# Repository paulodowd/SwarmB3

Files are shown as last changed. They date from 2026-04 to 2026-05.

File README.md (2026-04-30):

# SwarmB3

Working on Swarm Board version 3... so I decided the tinkering hadn't finished yet :)

Currently work in progress.  
- PCB in testing, version 4.
- Initial code drafted but a mess.

## Development Notes

**14/04/26:** Lots and lots of debugging between hardware and software.  The pcb design worked on the assumption that the UART tx could be inverted in software, as stated in the SAMD51 datasheet.  However, it doesn't work as I expected.  It seems to invert the data, but the idle state remains high.  This causes issues for IR communication because I don't want to saturate the environment with the carrier wave whilst communication is not occuring (idle high, AND'd with clock -> constant carrier wave transmission). I tried a software fix, pulling the gpio low between transmissions.  However, I can't seem to restore the GPIO properly without messing up the protocol overall. I got as far as seeing the bit pattern shifted by 1 bit, which is occuring because the receiver is mis-registering the start bit.  I tried leaving the GPIO alone, and only enabling/disabling the carrier wave, but the same problem is occuring.  When I look at both sides of the communication on the oscilloscope, I can see that for a batch send (like 10 bytes), the first byte is dropping the start bit.  I haven't been able to get to the bottom of why.  If I do not invert the tx, the problem goes away, but I don't want a non-inverted signal (saturation problem).  It could be that the essential problem is that inverting the Tx in SAMD51 doesn't invert the start and stop bits - the datasheet is unclear.  It simply says "start and stop unchanged", and I'm not sure if that means overall functionality or logic polarity.  It seems like the latter.  I tried some other logic gates.  Surprisingly, 74hc32 (OR) works as a drop in - however, it does mean that for data logic 1, the data stream is always on, and for data logic 0 actually an on/off pulse train - which is not ideal.  The receiver seems quite robust to this, the datasheet has measures for this sort of thing.  However, I don't want a board that could cause communication defects alongside from what I am investigating in research.  A possible fix is to implement active low LED drivers, which would necessitate an extra transister per UART (e.g. +4).  I don't fancy soldering that, so instead I've updated the pcb to pass tx outputs through a 74hc14 first.  I've tested this on breadboard and it works fine.  It means I can just use the UART interfaces normally without any software SAMD51 inversion.  The current code (ItsyBitsy_test) is a mess from all my debugging chopping and changes.  I'll refactor after testing the new pcb when it arrives.

**10/04/26:** The TSDP34156 is active low output when receiving an IR burst.  I had thought I would use the M4 SERCOM interface to invert the UART signal logic.  It seems like only the start,stop and data are inverted, but the idle signal remains high in either case. I spent some time trying to find a software solution to pull the tx line low, with no luck.  Even with no idle, or long bursts of transmission, I was getting gibberish on the receiving end regardless of whether I was inverting Tx or not.  With the assumption of inverting in software, the first pcb design had a 74hc08 AND gate to combine the 58khz clock and data.  Abandoning this, I first tried a NAND, but that actually just negates the effect of the clock - since a changing clock qualifies as not-and against data or no data.  Instead, an OR gate works. With Tx not inverted, if I draw out the truth table, then it means that for a data logic 0 a 58khz burst is created, and for data logic 1 a constant IR signal is made (not modulated, just on).     

**08/04/26:** Some pretty annoying problems with the first PCB prototype!  The 74hc08 ground was isolated.  The pots for current limiting were not in logical physical locations, not next to their LEDs.  I labelled the ItsyBitsy pin 7 wrong, so it wasn't conencted to the 74hc08.  Fixed all of that.  I've installed two different types of IR LEDs to compare the difference.  One is the Vishay TSAL4400 (https://www.vishay.com/en/product/81006/), and the other is an Onsemi QEE113 (https://www.onsemi.com/products/interfaces/infrared/emitting-diodes/qee113).  Both have similar characteristics, slightly different radiance patterns. I prefer the form factor of the Onsemi device.

**27/03/26:** Using the Adafruit SAMD51 board config, they have a wrapped class named sercom around the original defintions SERCOM (difference being lower and upper case).  I wanted to invert Tx (maybe Rx) and the Adafruit wrapper hasn't got this implemented yet.  These are useful links for low level structures and definitions for SERCOM (SAMD51 in general).
- https://github.com/ace22293/SAMD51/tree/master
- https://github.com/arduino/ArduinoCore-samd/tree/master/cores/arduino
- https://github.com/arduino/ArduinoModule-CMSIS-Atmel/tree/master/CMSIS-Atmel/CMSIS/Device/ATMEL/samd51/include/instance
- https://github.com/arduino/ArduinoModule-CMSIS-Atmel/tree/master/CMSIS-Atmel/CMSIS/Device/ATMEL/samd51/include

- **25/03/26:** Started the design of version 3 of the swarm board.  The plan is to use the Adafruit ItsyBitsy M4, providing a hardware UART interface for each IR reciever on the pcb. When drafting this PCB, I couldn't find a convenient symbol or footprint, so I've used two rows of pin headers and labels.  I also noticed that the symbol for the double row header for the M5Stack Core2 doesn't correspond with the physical footprint - but the enumeration is correct (just a bit confusing).

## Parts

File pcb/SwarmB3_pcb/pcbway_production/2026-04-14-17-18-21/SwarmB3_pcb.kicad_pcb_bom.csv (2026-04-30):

Designator | Quantity | Value | Footprint | Package | MPN | DNP | Mount_Type | Description | PROD_ID | Voltage | Tolerance | Field4
C1, C2 | 2 | 0.1uF | C_Disc_D4.7mm_W2.5mm_P5.00mm |  |  |  | tht | Unpolarized capacitor | CAP-25565 | 16V | 10%
D1_B1, D2_A1, D2_B1, D3_A1, D3_B1, D4_A1, D4_B1, D_1A1 | 8 | IR_LED | LED_D3.0mm_Horizontal_O1.27mm_Z2.0mm |  |  |  | tht
J1 | 1 | 5v_3Pi | PinHeader_1x02_P2.54mm_Vertical |  |  |  | tht |  |  |  |  | CONN-09863
J10 | 1 | ItsyBitsyRight | PinHeader_1x14_P2.54mm_Vertical |  |  |  | tht | Generic connector, single row, 01x14, script generated
J11 | 1 | ItsyBitsyLeft | PinHeader_1x14_P2.54mm_Vertical |  |  |  | tht | Generic connector, single row, 01x14, script generated
J2 | 1 | GND_3Pi | PinHeader_1x02_P2.54mm_Vertical |  |  |  | tht |  |  |  |  | CONN-09863
J3 | 1 | I2C_3V3_Exp | PinHeader_1x04_P2.54mm_Vertical |  |  |  | tht
J4 | 1 | Conn_02x15_M5Stack_Core2 | PinHeader_2x15_P2.54mm_Vertical |  |  |  | tht
J5 | 1 | I2C_3Pi | PinHeader_1x02_P2.54mm_Vertical |  |  |  | tht |  |  |  |  | CONN-09863
J6 | 1 | 3PI_SWTCH | PinHeader_1x02_P2.54mm_Vertical |  |  |  | tht |  |  |  |  | CONN-09863
J8 | 1 | ProxA | PinHeader_1x04_P2.54mm_Vertical |  |  |  | tht
J9 | 1 | ProxB | PinHeader_1x04_P2.54mm_Vertical |  |  |  | tht
PWR1, RESET1 | 2 | Bttn | SW_PUSH_6mm |  |  |  | tht
Q1, Q2, Q3, Q5 | 4 | PN2222A | TO-92_Inline |  |  |  | tht | 1A Ic, 40V Vce, NPN Transistor, General Purpose Transistor, TO-92
Q7, Q8 | 2 | 2N7000 | TO-92_Inline |  |  |  | tht
R1, R10, R13, R9 | 4 | 82R | R_Axial_DIN0204_L3.6mm_D1.6mm_P7.62mm_Horizontal |  |  |  | tht
R15, R16, R17, R18 | 4 | 1K | R_Axial_DIN0204_L3.6mm_D1.6mm_P7.62mm_Horizontal |  |  |  | tht
R19, R20 | 2 | 4k7 | R_Axial_DIN0204_L3.6mm_D1.6mm_P7.62mm_Horizontal |  |  |  | tht
R2, R3, R6 | 3 | LDR | R_LDR_5.0x4.1mm_P3mm_Vertical |  |  |  | tht
R4, R5, R7 | 3 | 10K_LDR | R_Axial_DIN0204_L3.6mm_D1.6mm_P7.62mm_Horizontal |  |  |  | tht
U1 | 1 | 74HC14 | DIP-14_W7.62mm_Socket |  |  |  | tht | Hex inverter schmitt trigger
U2 | 1 | 74LS08 | DIP-14_W7.62mm_Socket |  |  |  | tht | Quad And2
UD_1, UD_2, UD_3, UD_4 | 4 | TSDP34138 | Vishay_MOLD-3Pin |  |  |  | tht
VR2_A1, VR3_A1, VR4_A1, VR_1A1 | 4 | 5K_Pot_IRLED | Potentiometer_Bourns_3386P_Vertical |  |  |  | tht |  |  |  |  | RES-09730

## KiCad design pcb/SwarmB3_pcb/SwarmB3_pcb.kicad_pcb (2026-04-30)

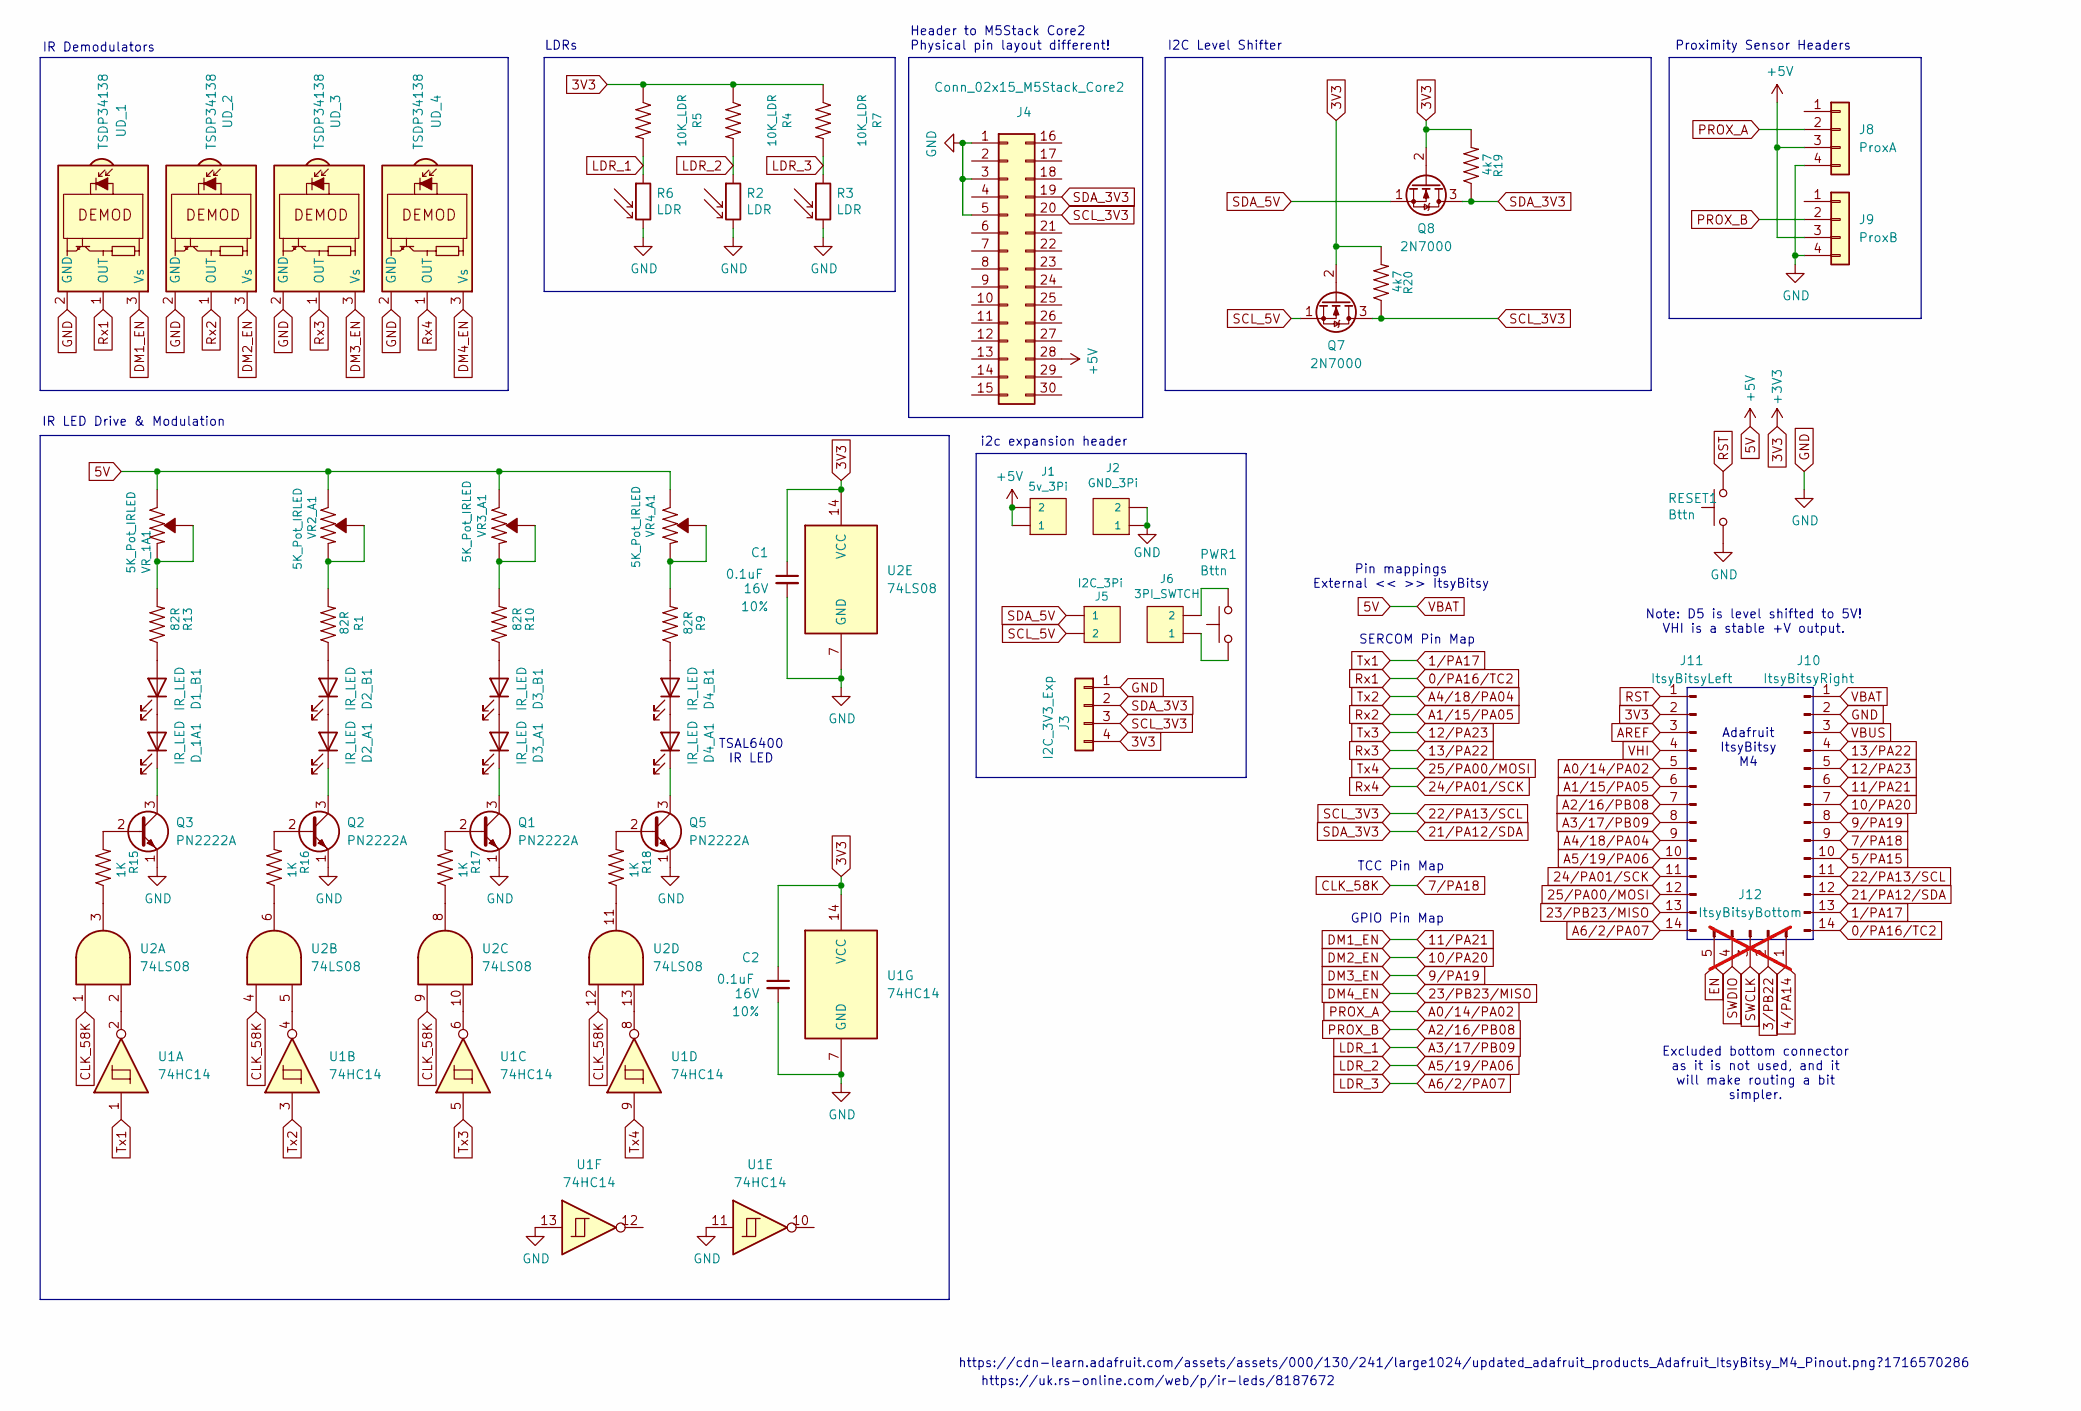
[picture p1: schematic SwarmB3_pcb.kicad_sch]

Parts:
C1, C2: 0.1uF; C_Disc_D4.7mm_W2.5mm_P5.00mm; Voltage 16V; Tolerance 10%
D1_B1, D2_A1, D2_B1, D3_A1, D3_B1, D4_A1, D4_B1: IR_LED; LED_D3.0mm_Horizontal_O1.27mm_Z2.0mm
D_1A1: IR_LED; LED_D3.0mm_Horizontal_O1.27mm_Z2.0mm
J1: 5v_3Pi; PinHeader_1x02_P2.54mm_Vertical
J2: GND_3Pi; PinHeader_1x02_P2.54mm_Vertical
J3: I2C_3V3_Exp; PinHeader_1x04_P2.54mm_Vertical
J4: Conn_02x15_M5Stack_Core2; PinHeader_2x15_P2.54mm_Vertical
J5: I2C_3Pi; PinHeader_1x02_P2.54mm_Vertical
J6: 3PI_SWTCH; PinHeader_1x02_P2.54mm_Vertical
J8: ProxA; PinHeader_1x04_P2.54mm_Vertical
J9: ProxB; PinHeader_1x04_P2.54mm_Vertical
J10: ItsyBitsyRight; PinHeader_1x14_P2.54mm_Vertical
J11: ItsyBitsyLeft; PinHeader_1x14_P2.54mm_Vertical
J12: ItsyBitsyBottom; not fitted
PWR1: Bttn; SW_PUSH_6mm
Q1, Q2, Q3, Q5: PN2222A; TO-92_Inline
Q7, Q8: 2N7000; TO-92_Inline
R1, R9, R10, R13: 82R; R_Axial_DIN0204_L3.6mm_D1.6mm_P7.62mm_Horizontal
R2, R3, R6: LDR; R_LDR_5.0x4.1mm_P3mm_Vertical
R4, R5, R7: 10K_LDR; R_Axial_DIN0204_L3.6mm_D1.6mm_P7.62mm_Horizontal
R15, R16, R17, R18: 1K; R_Axial_DIN0204_L3.6mm_D1.6mm_P7.62mm_Horizontal
R19, R20: 4k7; R_Axial_DIN0204_L3.6mm_D1.6mm_P7.62mm_Horizontal
RESET1: Bttn; SW_PUSH_6mm
U1: 74HC14; DIP-14_W7.62mm_Socket
U2: 74LS08; DIP-14_W7.62mm_Socket
UD_1, UD_2, UD_3, UD_4: TSDP34138; Vishay_MOLD-3Pin
VR2_A1, VR3_A1, VR4_A1: 5K_Pot_IRLED; Potentiometer_Bourns_3386P_Vertical
VR_1A1: 5K_Pot_IRLED; Potentiometer_Bourns_3386P_Vertical

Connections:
0/PA16/TC2: J10.14, UD_1.1 (OUT)
1/PA17: J10.13, U1.1
3V3: C1.1, C2.1, J3.4, J11.2, Q7.2 (G), Q8.2 (G), R4.1, R5.1, R7.1, R19.2, R20.2, U1.14 (VCC), U2.14 (VCC)
5V: J1.1, J1.2, J4.28, J8.3, J9.3, J10.1, VR2_A1.3 (CW), VR3_A1.3 (CW), VR4_A1.3 (CW), VR_1A1.3 (CW)
5/PA15: J10.10
7/PA18: J10.9, U2.1, U2.4, U2.9, U2.12
9/PA19: J10.8, UD_3.3 (Vs)
10/PA20: J10.7, UD_2.3 (Vs)
11/PA21: J10.6, UD_1.3 (Vs)
12/PA23: J10.5, U1.5
13/PA22: J10.4, UD_3.1 (OUT)
21/PA12/SDA: J3.2, J4.19, J10.12, Q8.3 (D), R19.1
22/PA13/SCL: J3.3, J4.20, J10.11, Q7.3 (D), R20.1
23/PB23/MISO: J11.13, UD_4.3 (Vs)
24/PA01/SCK: J11.11, UD_4.1 (OUT)
25/PA00/MOSI: J11.12, U1.9
A0/14/PA02: J8.2, J11.5
A1/15/PA05: J11.6, UD_2.1 (OUT)
A2/16/PB08: J9.2, J11.7
A3/17/PB09: J11.8, R5.2, R6.1
A4/18/PA04: J11.9, U1.3
A5/19/PA06: J11.10, R2.1, R4.2
A6/2/PA07: J11.14, R3.1, R7.2
AREF: J11.3
GND: C1.2, C2.2, J2.1, J2.2, J3.1, J4.1, J4.3, J4.5, J8.4, J9.4, J10.2, Q1.1 (E), Q2.1 (E), Q3.1 (E), Q5.1 (E), R2.2, R3.2, R6.2, RESET1.1, U1.7 (GND), U1.11, U1.13, U2.7 (GND), UD_1.2 (GND), UD_2.2 (GND), UD_3.2 (GND), UD_4.2 (GND)
unnamed: D1_B1.2 (A), R13.1
unnamed: D1_B1.1 (K), D_1A1.2 (A)
unnamed: D2_A1.2 (A), D2_B1.1 (K)
unnamed: D2_A1.1 (K), Q2.3 (C)
unnamed: D2_B1.2 (A), R1.1
unnamed: D3_A1.2 (A), D3_B1.1 (K)
unnamed: D3_A1.1 (K), Q1.3 (C)
unnamed: D3_B1.2 (A), R10.1
unnamed: D4_A1.2 (A), D4_B1.1 (K)
unnamed: D4_A1.1 (K), Q5.3 (C)
unnamed: D4_B1.2 (A), R9.1
unnamed: D_1A1.1 (K), Q3.3 (C)
unnamed: J6.1, PWR1.1
unnamed: J6.2, PWR1.2
unnamed: Q1.2 (B), R17.2
unnamed: Q2.2 (B), R16.2
unnamed: Q3.2 (B), R15.2
unnamed: Q5.2 (B), R18.2
unnamed: R15.1, U2.3
unnamed: R16.1, U2.6
unnamed: R17.1, U2.8
unnamed: R18.1, U2.11
unnamed: U1.2, U2.2
unnamed: U1.4, U2.5
unnamed: U1.6, U2.10
unnamed: U1.8, U2.13
unnamed: R1.2, VR2_A1.1 (CCW), VR2_A1.2 (WIPER)
unnamed: R10.2, VR3_A1.1 (CCW), VR3_A1.2 (WIPER)
unnamed: R9.2, VR4_A1.1 (CCW), VR4_A1.2 (WIPER)
unnamed: R13.2, VR_1A1.1 (CCW), VR_1A1.2 (WIPER)
RST: J11.1, RESET1.2
SCL_5V: J5.2, Q7.1 (S)
SDA_5V: J5.1, Q8.1 (S)
VBUS: J10.3
VHI: J11.4

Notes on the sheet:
IR LED Drive & Modulation
IR Demodulators
Pin mappings External << >> ItsyBitsy
Proximity Sensor Headers
GPIO Pin Map
I2C Level Shifter
Adafruit ItsyBitsy M4
SERCOM Pin Map
Header to M5Stack Core2 Physical pin layout different!
https://uk.rs-online.com/web/p/ir-leds/8187672
TCC Pin Map
Note: D5 is level shifted to 5V! VHI is a stable +V output.
https://cdn-learn.adafruit.com/assets/assets/000/130/241/large1024/updated_adafruit_products_Adafruit_ItsyBitsy_M4_Pinout.png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
LDRs
Excluded bottom connector as it is not used, and it will make routing a bit simpler.
i2c expansion header
TSAL6400 IR LED

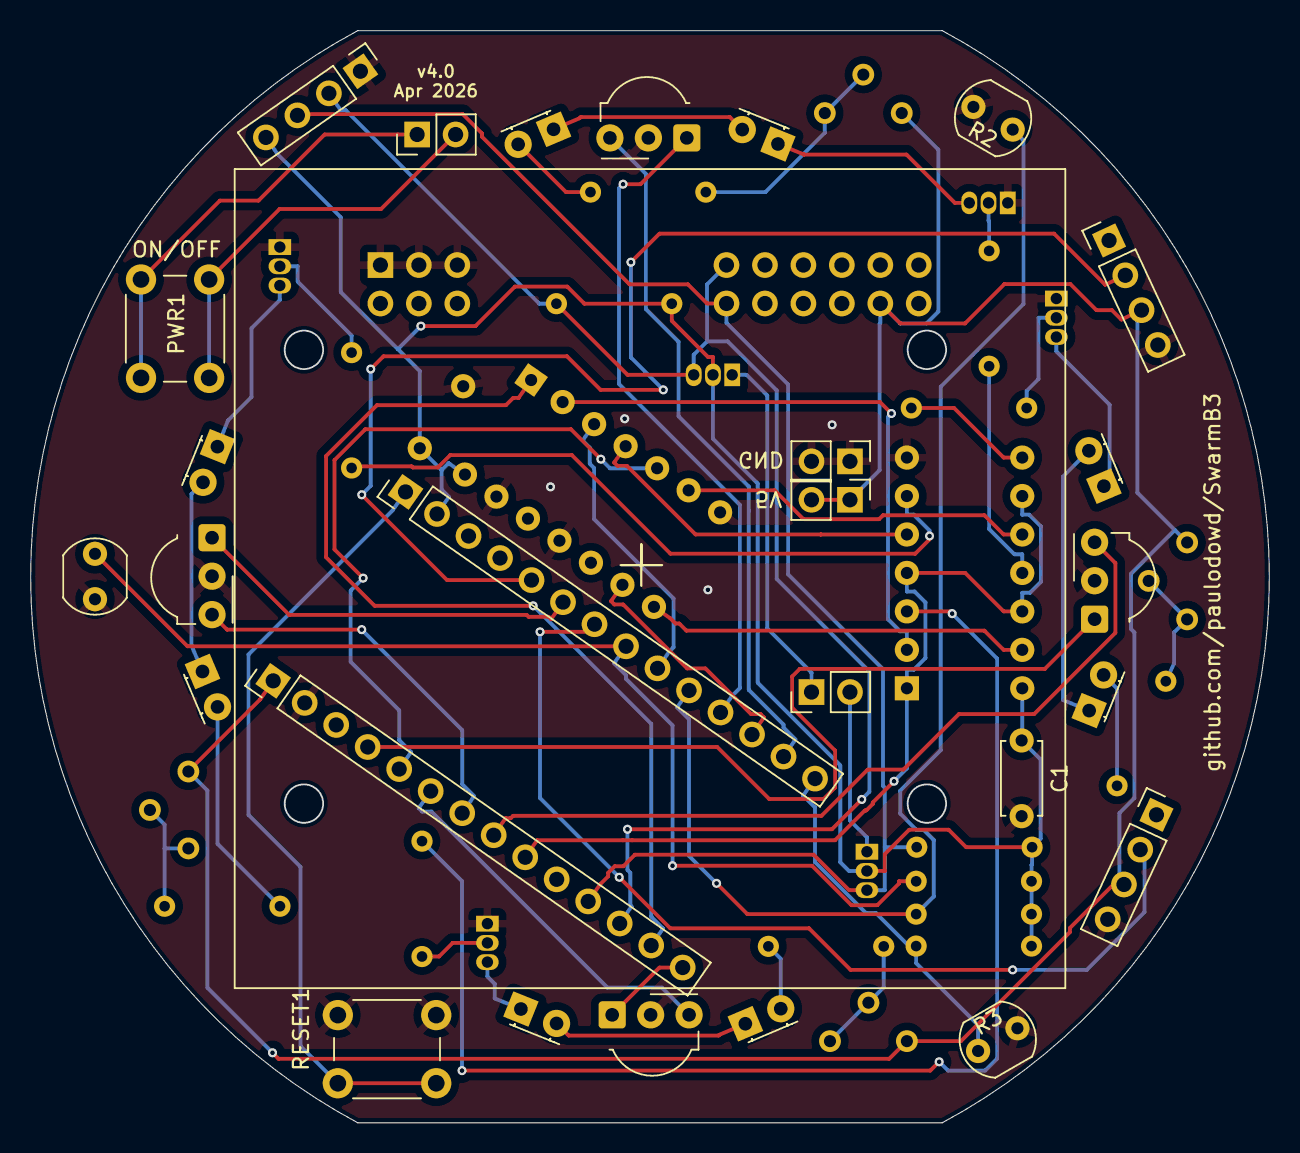
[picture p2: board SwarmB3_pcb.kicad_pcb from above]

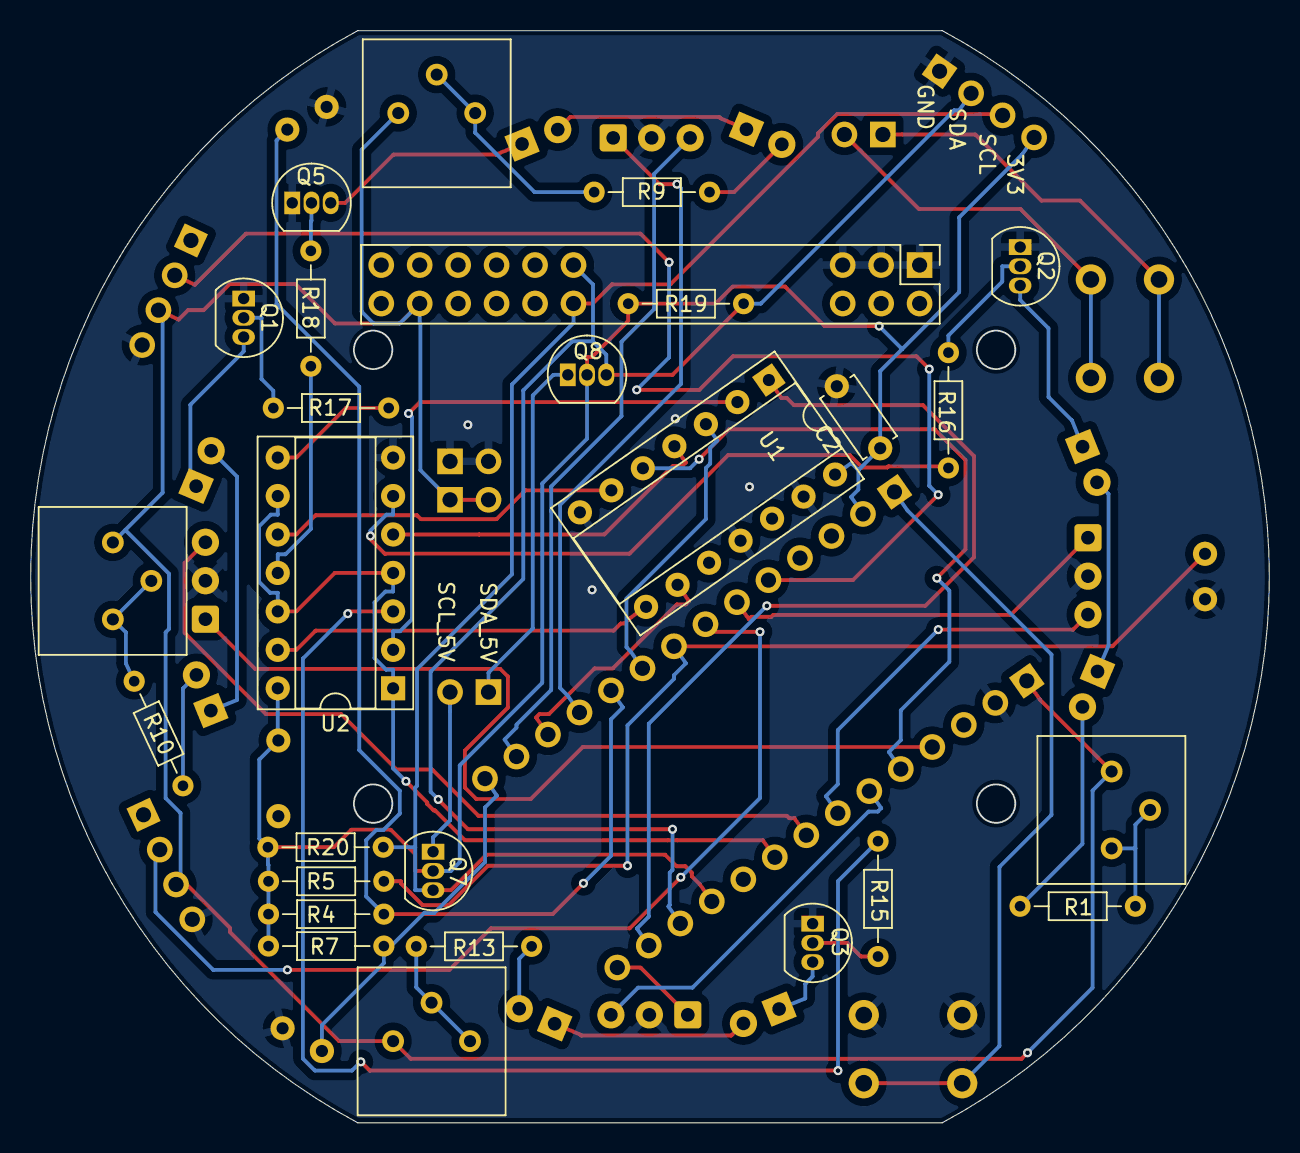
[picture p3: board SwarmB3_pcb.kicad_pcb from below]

Board: 2 copper layers, 81.8 x 72.1 mm, 54 parts (27 on the bottom side), 56 nets.

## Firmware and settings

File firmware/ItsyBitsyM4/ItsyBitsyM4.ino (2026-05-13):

/* To do:
*/



#include <Arduino.h>
#include <wiring_private.h>
#include <Wire.h>

//#include "sam.h" // for SAMD51 registers
#include "ircomm.h"
#include "sercom_funcs.h"
#include "ir_parser.h"
#include "ircomm_i2c.h"

// GPIO mappings
#define PROXA_IN_PIN  PIN_PA02
#define PROXB_IN_PIN  PIN_PB08
#define LDRA_IN_PIN   PIN_PB09
#define LDRB_IN_PIN   PIN_PA06
#define LDRC_IN_PIN   PIN_PA07





void setup() {

  Serial.begin(115200);

  // Paul: debugging 10/05/26
//  while (!Serial);
//  Serial.println("Reset");


  randomSeed( generateRandomSeed() );


  pinMode( DEMOD1_EN_PIN, OUTPUT);
  pinMode( DEMOD2_EN_PIN, OUTPUT);
  pinMode( DEMOD3_EN_PIN, OUTPUT);
  pinMode( DEMOD4_EN_PIN, OUTPUT);

  // 58 kHz output on D4
  setup58kHz();

  fullReset();

  // Activate SERCOM units. Note, slightly
  // different config for each.
  // TODO: update baud from config
  pinPeripheral(0, PIO_SERCOM);
  pinPeripheral(1,  PIO_SERCOM);
  port_D1_D0.begin(BAUD);

  //  // UART4: MOSI TX / SCK RX -> SERCOM1 (SCK is 24, MOSI is 25)
  pinPeripheral(24, PIO_SERCOM_ALT);
  pinPeripheral(25,  PIO_SERCOM_ALT);
  port_D25_D24.begin(BAUD);

  // UART3: D12 TX / D13 RX -> SERCOM5
  pinPeripheral(12, PIO_SERCOM_ALT);
  pinPeripheral(13, PIO_SERCOM_ALT);
  port_D12_D13.begin(BAUD);

  // Had trouble with this one!
  beginSerialA4A1_manual(BAUD);



  Wire.begin(IRCOMM_I2C_ADDR);
  Wire.onReceive( i2c_receive );
  Wire.onRequest( i2c_request );

  //  // Paul: debugging 10/05/26
//  for ( int i = 0; i < 4; i++ ) {
//    config.tx[0].repeat = UINT32_MAX;
//    config.tx[0].preamble_repeat = 0;
//  }
//  config.general.flags.bits.broadcast = 1;
//  setTestMessage(4);
//    Serial.println("Setup complete");

}

uint32_t generateRandomSeed() {
  uint32_t seed = 0x00000000;
  pinMode(A3, INPUT);

  // Generate an unsigned long as a seed by reading
  // the lsb of an analogRead.
  for ( int i = 0; i < 32; i++ ) {
    uint32_t sample = (uint32_t)analogRead(A3);
    sample = (sample & 0x00000001) << i;
    seed |= sample;
    delay(1);
  }
  return seed;
}

void setTestMessage(int len) {

  char msg[34];
  memset( (char*)msg, 0, sizeof( msg ));
  for ( int j = 0; j < len; j++ ) {

    char c;
    do {
      c = (char)random(0, 255);
    } while ( c == '~' || c == '^' );
    msg[j] = c;
  }
  for ( int i = 0; i < 4; i++ ) {
    memset( (uint8_t*)config.tx_buf[i], 0, sizeof( config.tx_buf[i] ));
    config.tx[i].len = parser[i].formatIRMessage( (uint8_t*)config.tx_buf[i], (uint8_t*)msg, strlen(msg));
  }


}


static unsigned long alive_ts;
void loop() {
  
  handleI2cFlags();
  handleMsgParsing();
  handleDemodulatorSaturation();
  handleBearingEstimation();
  handleTransmit();
}

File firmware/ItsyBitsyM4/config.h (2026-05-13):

// 27/03/26: I've directly copied this in from Swarm-B2 without
// changes so this will need a revision. Many fields don't 
// make sense for SwarmB3

// The following provide the default configuration
// of the communication board.

#ifndef IRCOMM_CONFIG_H
#define IRCOMM_CONFIG_H


/*
 * General (top-level) config
 */
#define BAUD                    9600
#define BROADCAST               1
#define BIDIRECTIONAL           0 
#define BEARING_UPDATE_US       10000 // 100ms
#define BEARING_ALPHA           0.25  // 
#define TX_PREAMBLE_BYTE        0x55 // 0b01010101, 'U'


/*
 * Config assigned to each receiver
 */
#define RX_OVERRUN              true  // allow for rx message to complete? 
#define RX_ENABLED              1
#define RX_TIMEOUT_MULTI        15    // 1200us, 1.2ms
#define RX_SATURATION_US        8000 // 8ms no bytes
#define RX_DESATURATION_US      2000 // off for 2ms

/*
 * Config assigned to each transmitter
 */
#define TX_INTERVAL_MOD         0
#define TX_REPEAT               1
#define TX_PREDICT_MULTI        0
#define TX_DEFER_MULTI          0
#define TX_PREAMBLE_REPEAT      0
#define TX_INTERVAL_MS          1
#define TX_BASE_MS              1
#define TX_LEN                  0






#endif

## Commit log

2026-03-25 pcb design prior to prototyping
    [SwarmB3_pcb-B_Cu.gbr, SwarmB3_pcb-B_Fab.gbr, SwarmB3_pcb-B_Mask.gbr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]
2026-03-25 added some development notes, removed old files
    [SwarmB3_pcb-B_Cu.gbr, SwarmB3_pcb-B_Fab.gbr, SwarmB3_pcb-B_Mask.gbr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]
2026-03-27 add initial test code for itsybitsy
    [SwarmB3_pcb.kicad_sch]
2026-03-27 Implemented frame error counting and helpers.
2026-03-28 stripping back and rationalising the datatypes/structures for this new board where we no longer need to poll receivers. That means timing information for rx is now obsolete. The only thing that matte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
    [config.h, ir_parser.cpp, ir_parser.h]
2026-03-30 Counldn't get SERCOM0 to work with standard approach. Had to do a manual init then use the Arduino Uart class afterwards. Tested working. Daisy chained tx to rx around all 4 uart interfaces.
2026-03-31 tested i2c on default pins and a 58khz signal on pin 7, both working.
    [SwarmB3_pcb.kicad_sch]
2026-04-01 moved sercom functions into their own source files.
    [SwarmB3_pcb.kicad_pcb_bom.csv, SwarmB3_pcb.kicad_pcb_positions.csv]
2026-04-08 Found errors with the PCB, fixed. Pin 7 was labelled wrong, so it wasn't connected to the 74HC08. 3 of the pots were located in illogical places, not next to the associated LEDs. The 74HC08 was also 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
    [SwarmB3_pcb.kicad_pcb, SwarmB3_pcb.kicad_pcb_bom.csv, SwarmB3_pcb.kicad_pcb_positions.csv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]
2026-04-08 Revise development notes for swarm board version 3
    Updated development notes for version 3 of the swarm board, detailing issues with the first PCB prototype and comparisons of IR LEDs.
2026-04-09 Somehow, I had the pcb manufactured with A1 as rx for a UART, but my latest design files were for A5. Since I've debugged and tested the PCB as working, I've modified the design files back to using A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
    [SwarmB3_pcb.kicad_pcb, SwarmB3_pcb.kicad_sch]
2026-04-14 Lots and lots of debugging between hardware and software. The pcb design worked on the assumption that the UART tx could be inverted in software, as stated in the SAMD51 datasheet. However, it doesn'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
    [SwarmB3_pcb.kicad_pcb, SwarmB3_pcb.kicad_pcb_bom.csv, SwarmB3_pcb.kicad_pcb_positions.csv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]
2026-04-24 add in non-blocking functionality to toggle the demodulators on and off for a short period to remove the effect of the automatic gain control saturating when there is no carrier signal. ALtered the p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
    [SwarmB3_pcb.kicad_pcb, SwarmB3_pcb.kicad_pcb_bom.csv, SwarmB3_pcb.kicad_pcb_positions.csv]
2026-04-24 Fixed a bug with the parser getNextByte() function. For any intermediate byte in a payload, it wasn't returning a 1-byte value, meaning that the activity log was always too few. I could see a 9 byte 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
    [ir_parser.cpp, ir_parser.h]
2026-04-25 cleaned up config.h, then implemented calls to the config through the code. Implemented disabling Rx during a transmit. Implemented non-blocking transmit. Decided to add a 3rd demod state, so active,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
    [config.h, sercom_funcs.cpp, sercom_funcs.h]
2026-04-26 Converted tx_timings timestamps back to milliseconds. I think we are getting roughly 1ms per byte transmitted out of UART, and I don't think higher precision than that is useful. I've started to impl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
2026-04-26 broadcast transmit framework in
2026-04-26 Found an interesting limitation I hadn't considered with Swarm-B2. The Serial.write() function is blocking whilst there are not enough bytes free in the buffer. I don't want this operation to block. 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
2026-04-27 implemented and test broadcast tx and individual tx. Implemented tx timing configuration and desync - both tested. Implemented defer but not yet tested. Implemented rx overrun but not yet tested. Ove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
    [config.h, ir_parser.cpp, ir_parser.h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]
2026-04-27 tested all functionality. Seems to be working. The remaining task is to populate the i2c request/receive functions. Built a second board and tested transmit between them. Small refactor, moved all ma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
2026-04-29 implemented i2c functionality. Tested against a master side SwarmB3_c class implementation to make i2c calls. Not everything is fully tested yet. Message sending and receiving is tested. Getting conf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
2026-04-30 caught a bug: had the wrong SERCOM identified in the frame count ISR for D0/D1 (SERCOM3). Also had a related bug in the i2cUpdateFrameCount() function. Implemented Pololu side functions to read over 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
    [ItsyBitsyM4.ino, ircomm.cpp, ircomm_i2c.cpp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]
2026-04-30 added a new i2c data struct to count both the instances of transmission and the instances of deferred transmission. Tested working on the pololu side.
2026-05-10 Caught a bug when the board was configured for broadcast. memcpy was used from 0 to other channels, but the for loop stopped 1 short.
    [ItsyBitsyM4.ino, config.h, ircomm.cpp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]
2026-05-11 Found and fixed an interesting bug. When doing a broadcast transmission, the function attemptMsgWriteToSerialBuffer() was filling up the entire serial buffer, and this was taking up to approx 250us. 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
    [ItsyBitsyM4.ino, ircomm.cpp]
2026-05-13 Issue#3: amended the IRParser_c class to include the CRC in the escaping. Tested working.
    [ItsyBitsyM4.ino, ir_parser.cpp, ircomm.cpp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]
2026-05-13 moved byte time out check in parser class over to microseconds, and so changed timeout_multi config parameter to be multiples of 100us. Found a bug with b_masked, fixed that.
    [ItsyBitsyM4.ino, config.h, ir_parser.cpp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]
